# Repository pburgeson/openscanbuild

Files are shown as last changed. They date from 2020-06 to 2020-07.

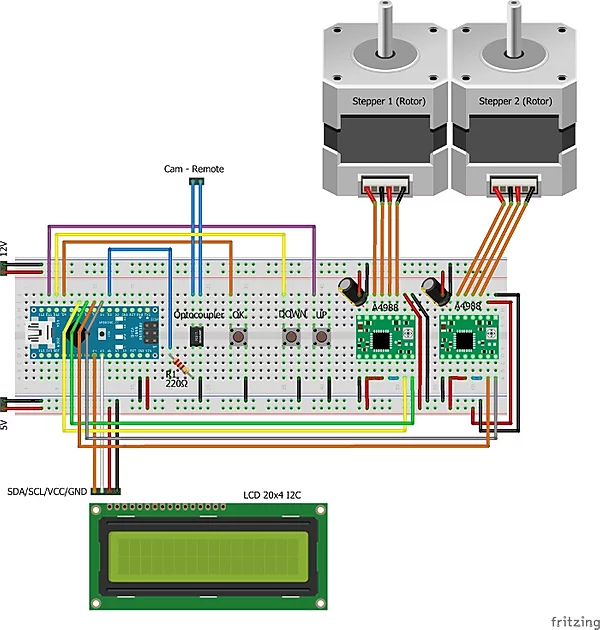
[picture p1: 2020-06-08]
Electronics/Breadboard - Schaltplan.webp

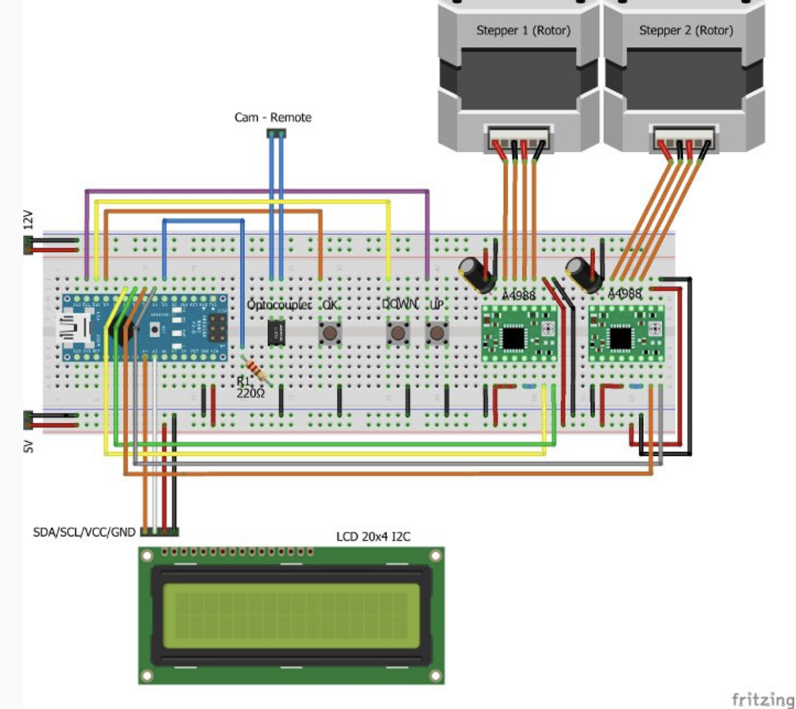
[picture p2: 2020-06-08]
Electronics/Openscan-fritzing.png

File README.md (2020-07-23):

# 3D Scanner Build
Build and testing of 3D scanner from Open Scan (https://en.openscan.eu/).  This is just using their plans and documents to successfully build a 3d scanner that uses photogrammetry.  My primary intent is to not have to measure objects that I want to design around in CAD.  Typically that means I'll be 3D printing the parts that make with it so precision is not incredibly critcal.  If I can get with +/- 0.010 in, I'll be pretty happy. 

A secondary goal is to develop processes and methods for updating github with project info and something akin to a project log.

# High Level Requirements
1. Able to generate 3D data that Autodesk Fusion 360 is capable of working with.
2. Precision of 0.010" or better
3. Scan Volume - Cylinder of 12 in diameter and height of 8 in
4. ~~Use of trinamic stepper drivers~~*
*Removed as open scan pcb was not compatible with Trinamic Step Stick and does not affect functionality

Future projects will include substantially more requirements development.  Since this project is about building a thing that someone else's design and documenting it, we won't go into a lot more detail.

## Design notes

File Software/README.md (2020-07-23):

# openscanbuild Software
2019_06-01_Scanner.ino - Arduino Sketch from openscan.eu
AccelStepper-1.59.zip - Arduino library for driving a stepper motor
NewLiquidCrystal_1.5.1.zip - Arduino library for lcd display
Scanner_Software_No_IRShutter - Arduino Sketch removing IR shutter due to difficulty in finding library
stepper_drive_step_dir_test - testing of stepper motor drive

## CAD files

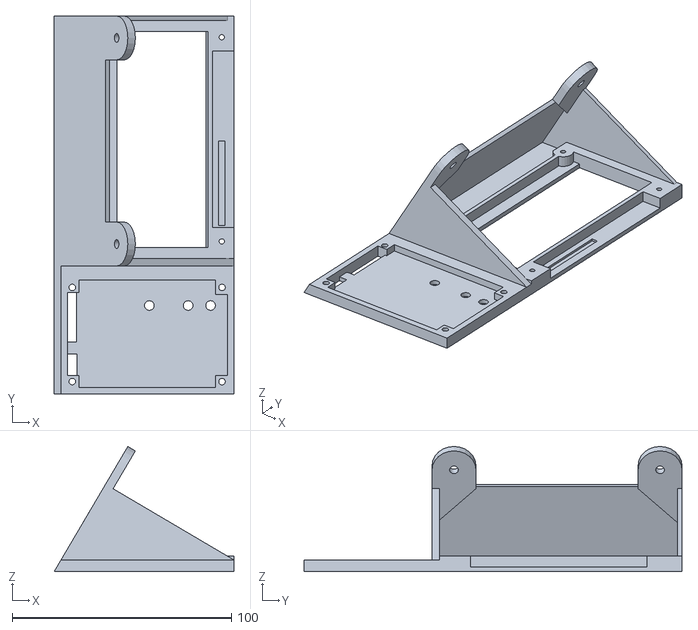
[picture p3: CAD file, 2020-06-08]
CAD Files/Control_module.stl
81.9 x 172.2 x 57.0

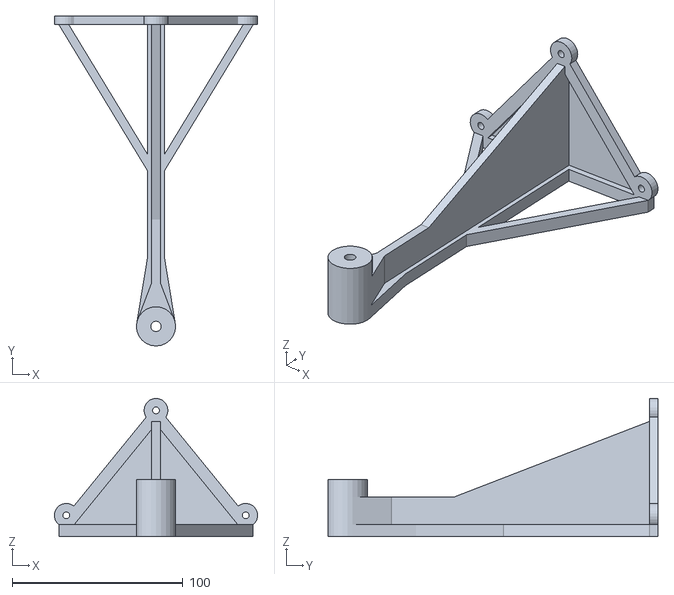
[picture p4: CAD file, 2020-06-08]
CAD Files/Stand2.stl
119.0 x 193.3 x 80.9

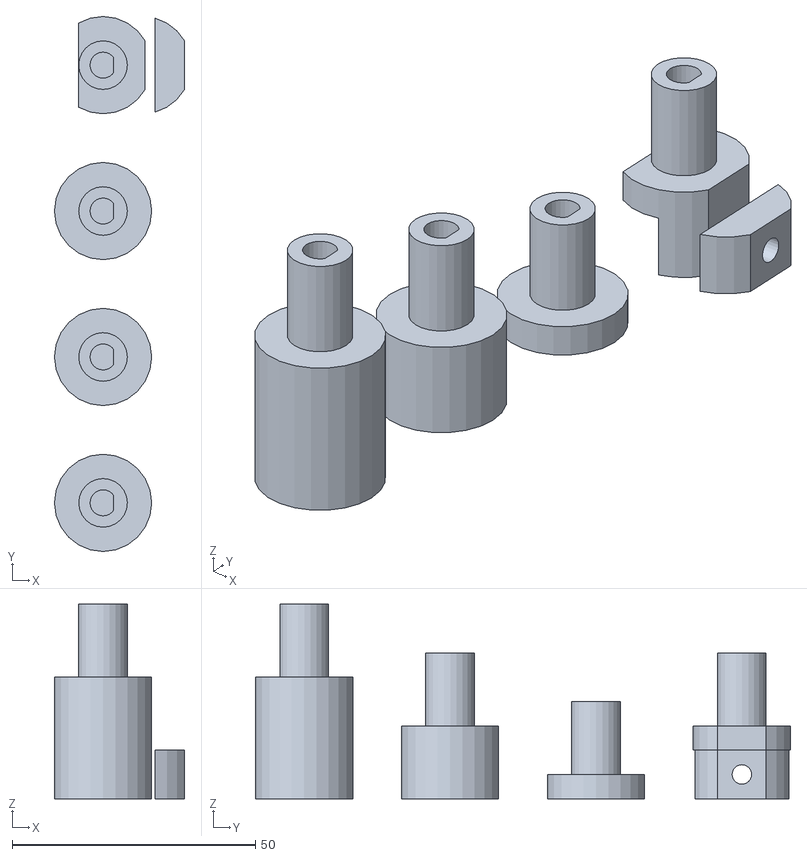
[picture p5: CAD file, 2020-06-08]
CAD Files/Turntable_-_Adapter_small.stl
26.8 x 110.0 x 40.0

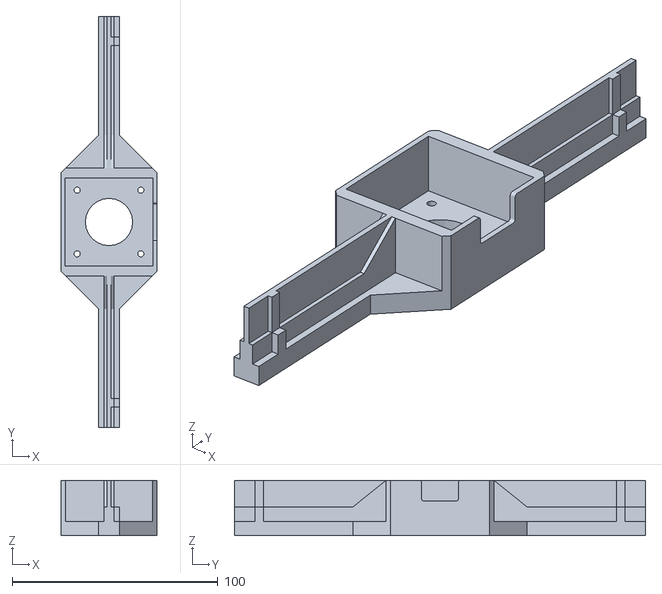
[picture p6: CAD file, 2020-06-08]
CAD Files/Turntable_Base_smallNema.STL
46.6 x 200.0 x 27.0

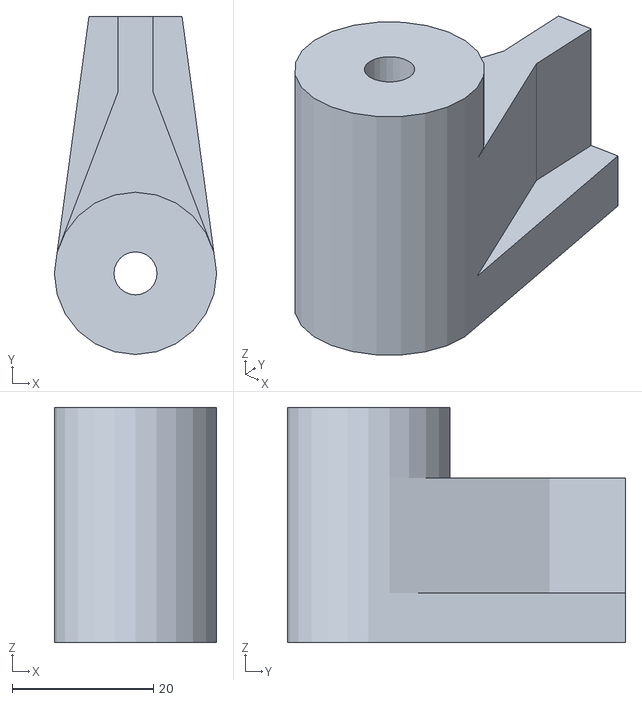
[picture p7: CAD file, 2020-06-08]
CAD Files/Stand1_-_Nema17 - Top.stl
23.0 x 47.9 x 33.3

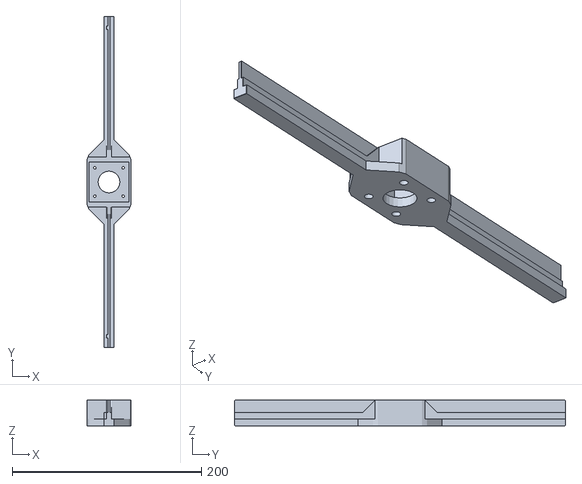
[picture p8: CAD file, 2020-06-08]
CAD Files/Turntable_Base_large_version_35cm.stl
47.0 x 350.0 x 27.0

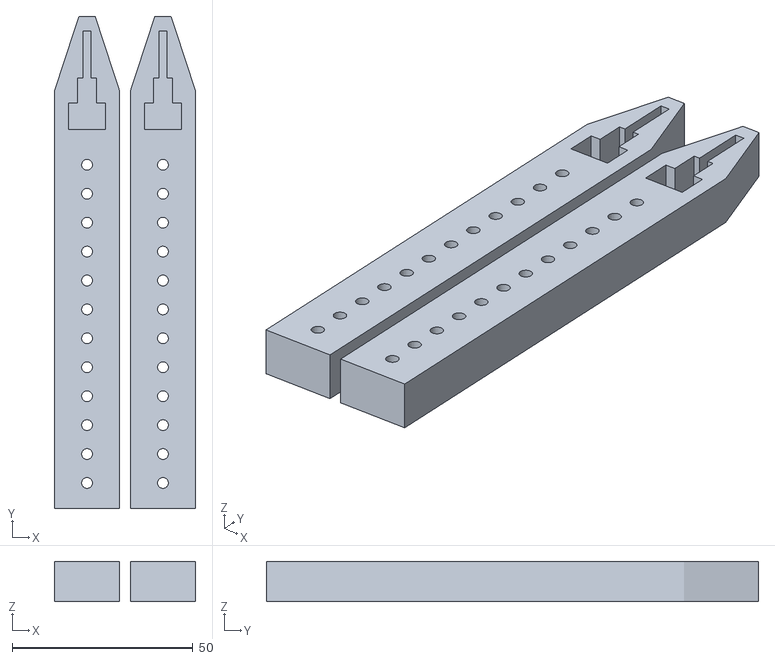
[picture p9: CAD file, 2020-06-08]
CAD Files/Rotary_Arm_-_2x.stl
39.0 x 136.2 x 11.2

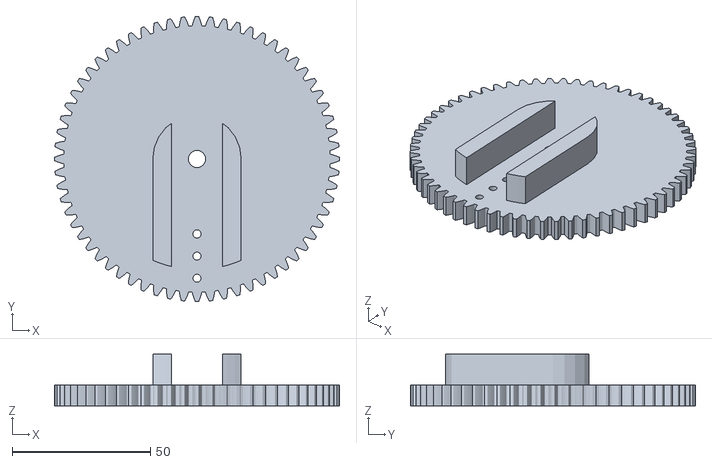
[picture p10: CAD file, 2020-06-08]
CAD Files/Adapter2_-_Gear_large.stl
103.1 x 103.1 x 18.7

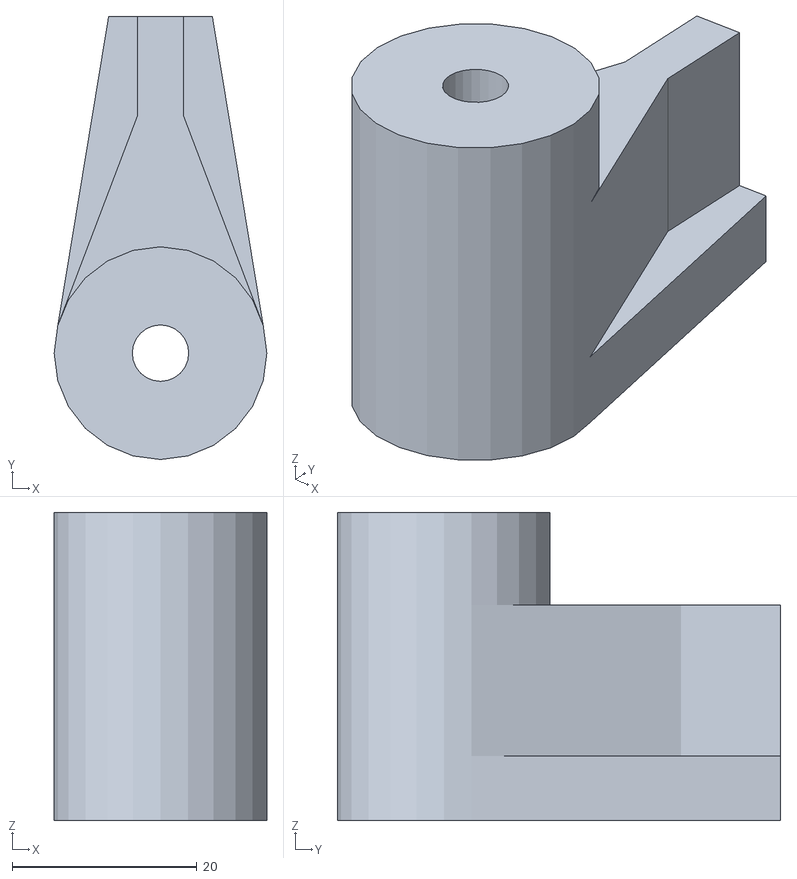
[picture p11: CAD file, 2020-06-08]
CAD Files/Stand2 - Top.stl
23.0 x 47.9 x 33.3

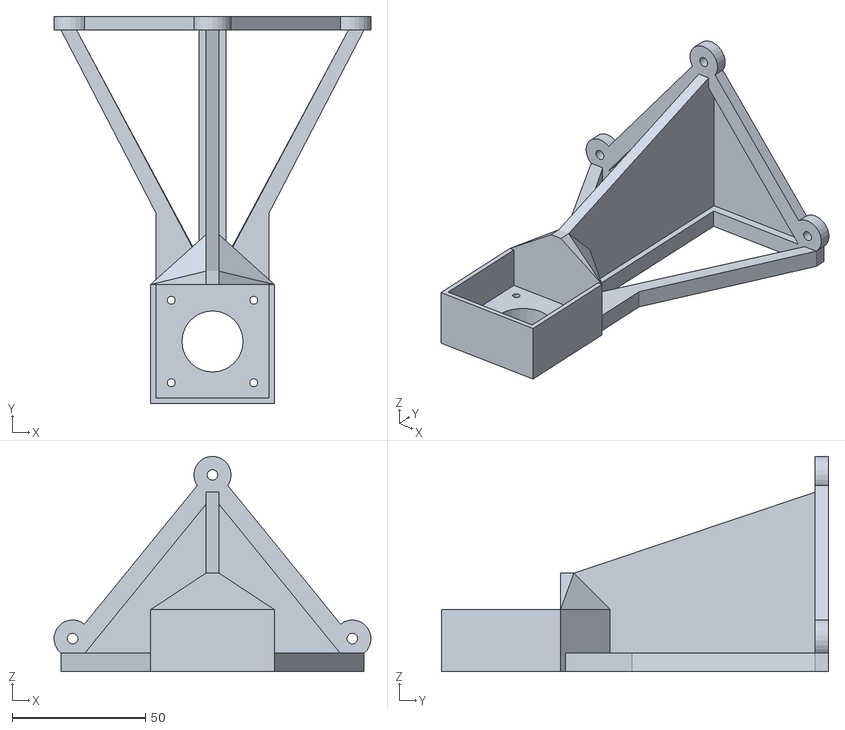
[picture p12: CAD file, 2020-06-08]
CAD Files/Stand1_-_Nema17 - Short.stl
119.0 x 145.4 x 80.9

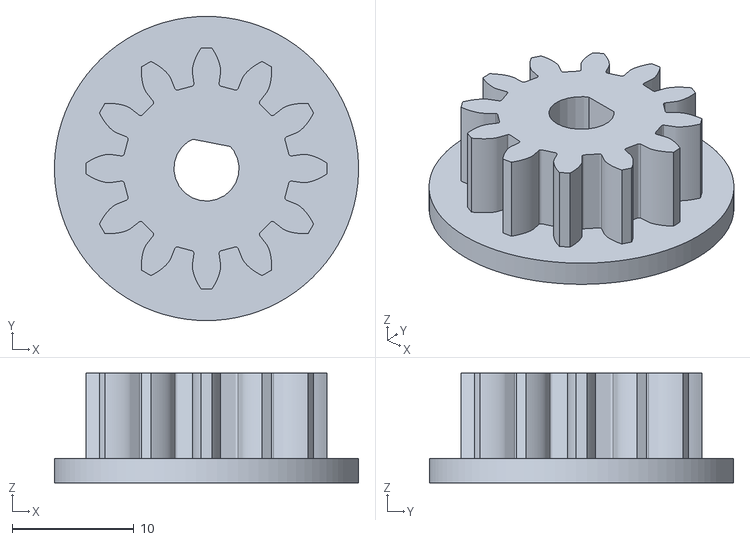
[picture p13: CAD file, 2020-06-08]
CAD Files/Gear_-_Small_v2.stl
25.0 x 25.0 x 9.00

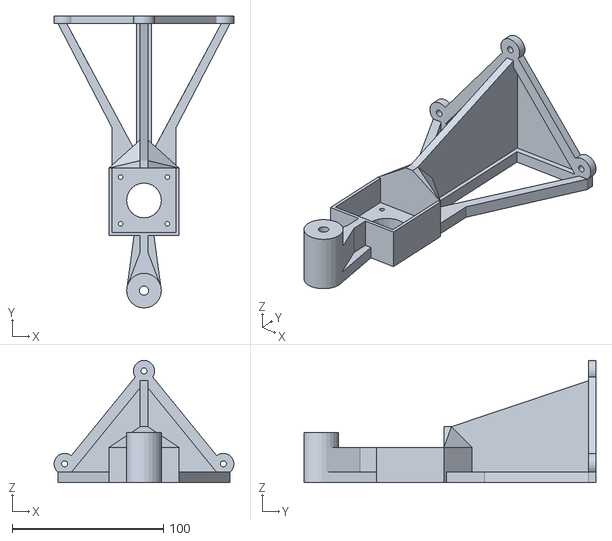
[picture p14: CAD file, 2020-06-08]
CAD Files/Stand1_-_Nema17.stl
119.0 x 193.3 x 80.9

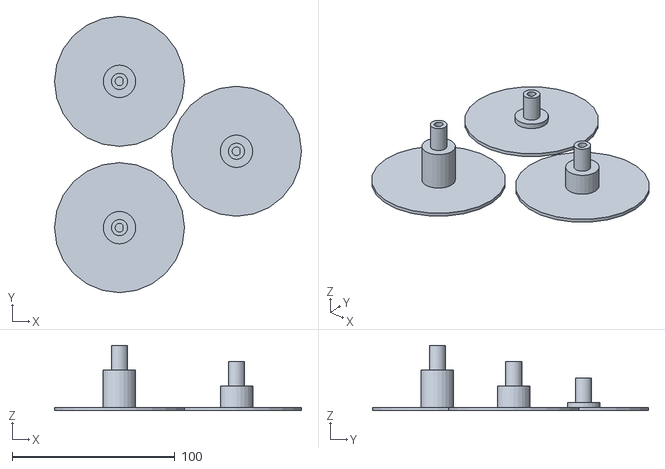
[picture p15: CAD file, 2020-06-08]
CAD Files/Turntable_-_Adapter_large.stl
152.0 x 170.0 x 40.0

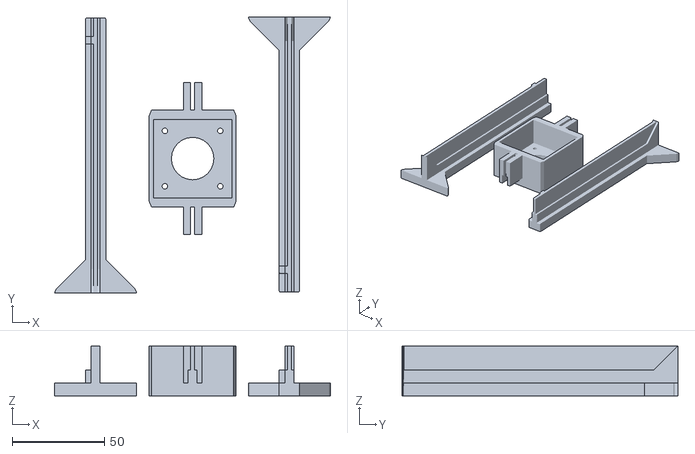
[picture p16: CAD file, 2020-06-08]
CAD Files/Turntable_Base_Large_Version_35cm_split_version_by_Paul.stl
149.4 x 149.3 x 27.0

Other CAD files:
CAD Files/Stand2 - Short.stl
CAD Files/Adapter1.stl
CAD Files/Gear_-_Small_v1.stl
CAD Files/Stand1_-_Nema17 v4.f3d
CAD Files/Stand2 v3.f3d

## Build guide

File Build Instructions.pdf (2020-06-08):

# OpenScan – User Manual

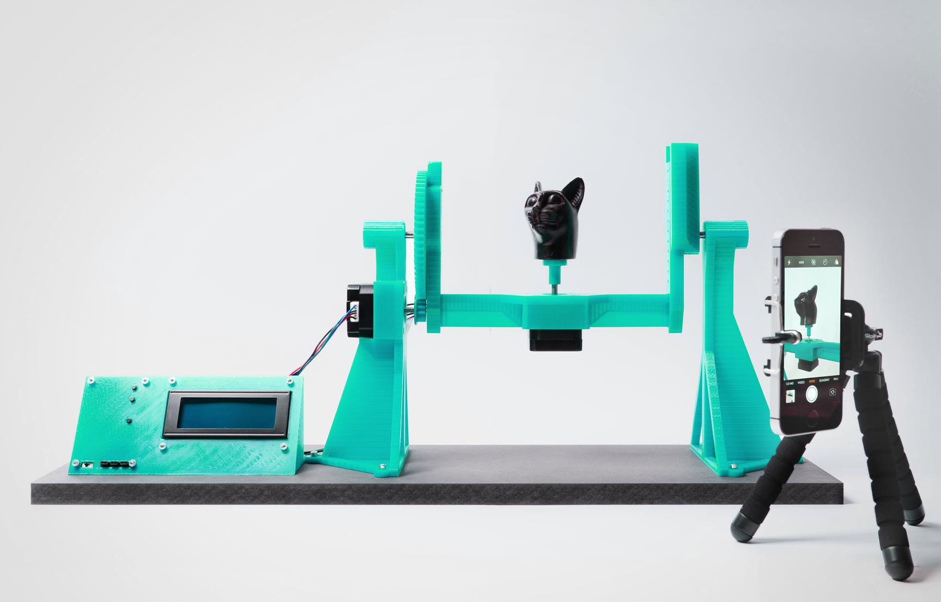
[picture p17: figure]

## Contents

## Material needed

M3 nut | 8
M3x12mm | 10
M3x8mm | 8
Steel pin (d=6mm, l>50mm) | 2
Jumper Wire 10cm m-f | 4
Nema 17 (min. 40Ncm) | 2
Stepper motor cable >70cm JST-XH-4P or 4P DuPont | 2
LCD 20x4 with I2C-Module | 1

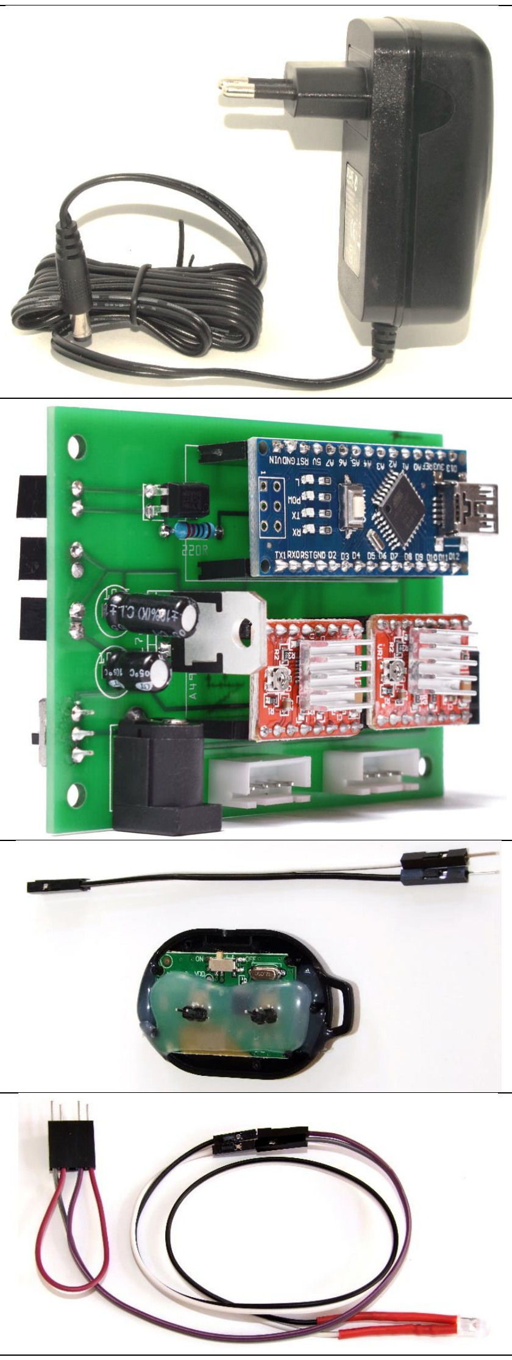
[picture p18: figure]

Power Supply 12V 2A Barrel connector (5,5mm-2,5mm) | 1
Control unit | 1
Remote Control Bluetooth (optional) | 1
Remote Control Infrared (optional) | 1

3D printable parts(https://www.thingiverse.com/thing:3050437/files)

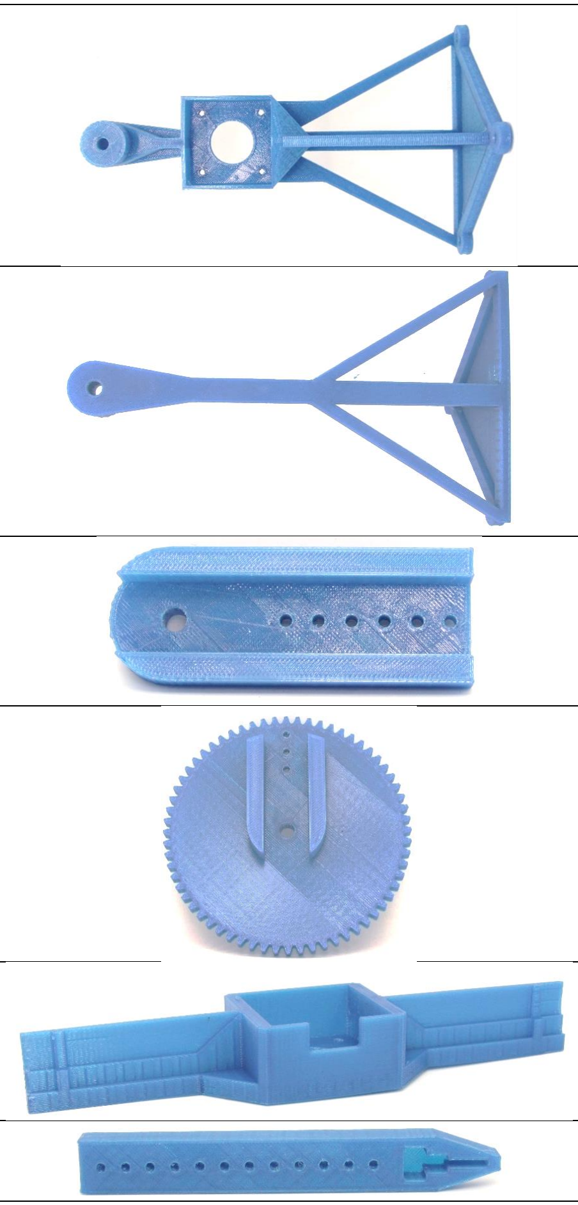
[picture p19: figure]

Stand1_Nema17.stl | 1
Stand2.stl | 1
Adapter1.stl | 1
Adapter2.stl | 1
Turntable_Base_Small.stl Optional:large-version | 1
Rotary_Arm.stl | 2

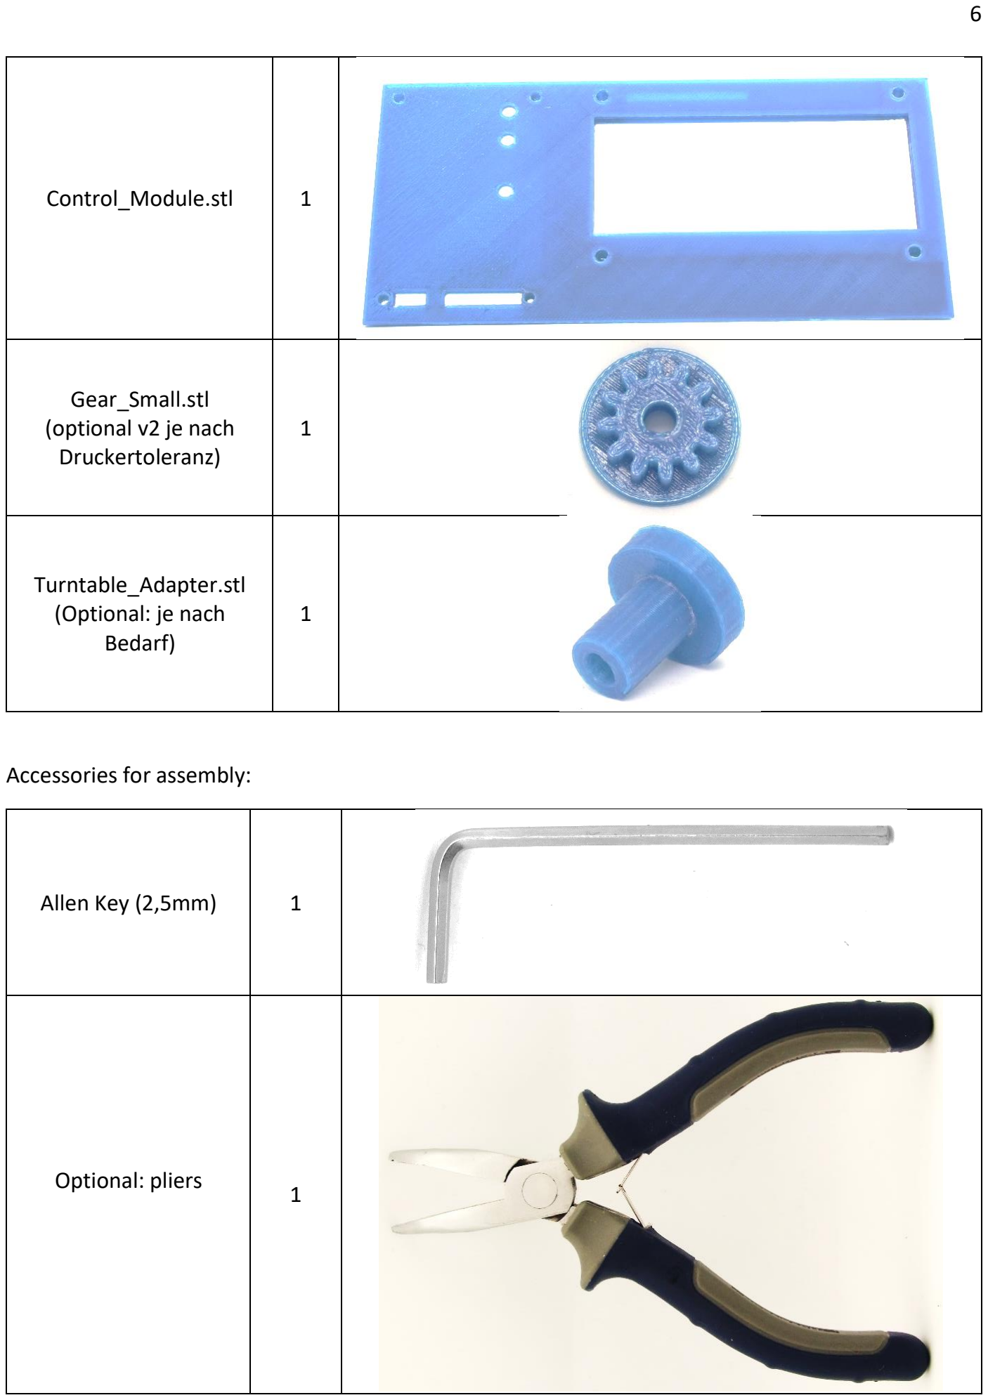
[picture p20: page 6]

Control_Module.stl | 1
Gear_Small.stl (optional v2 je nach Druckertoleranz) | 1
Turntable_Adapter.stl (Optional: je nach Bedarf) | 1

Accessories for assembly:

Allen Key (2,5mm) | 1
Optional: pliers | 1

## Assembly

### Step 1 – LCD

Needed parts:

- LCD 20x4 with I2C-Modul
- Control_module.stl
- M3x12 (4x)
- M3 nuts (4x)

Front:

Back:

Description:

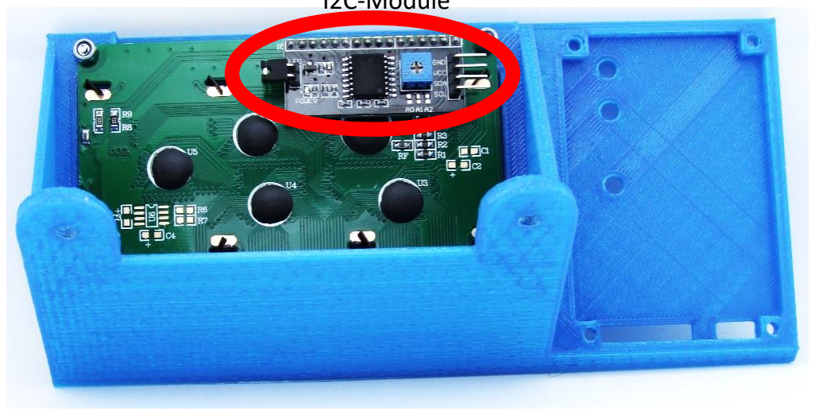
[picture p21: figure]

The display is mounted on the back of the control unit using four of the M3x12mm screws. See the orientation of the display - I2C module top right.

Note:

Depending on the printing accuracy, it may be necessary to pre-drill the screw holes with a 3mm drill bit.

I2C-Module

### Step 2 – Control unit

Needed parts:

- Control unit
- Control_module.stl (nach Schritt 1)
- M3x12 (4x)
- M3 nuts (4x)

Front:

Back:

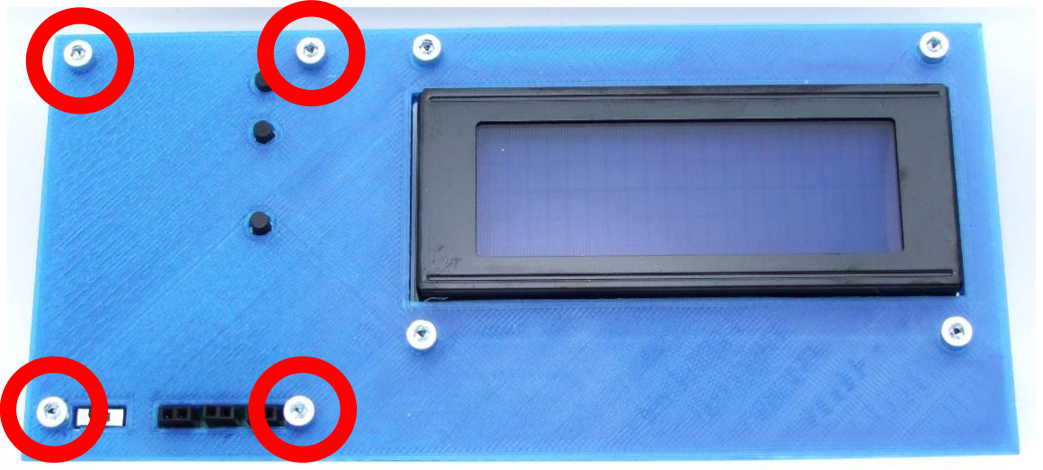
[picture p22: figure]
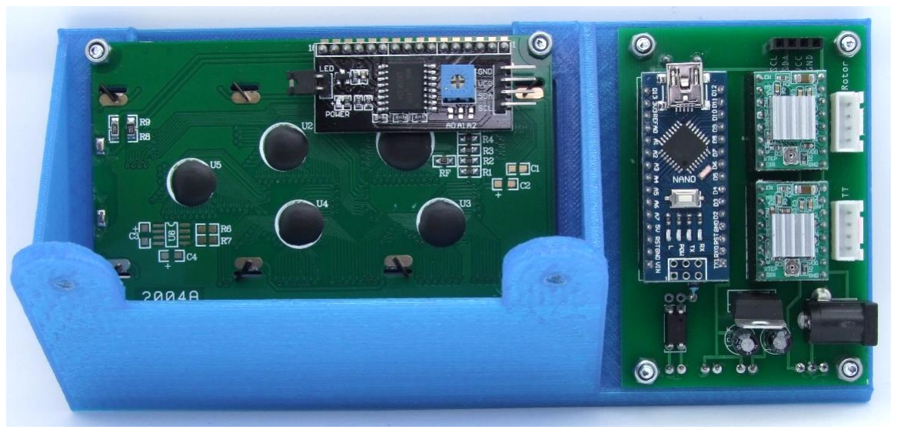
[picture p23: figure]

Description:

The control unit is mounted on the back of the printed unit using four of the M3x12mm screws.

Note:

Depending on the printing accuracy, it may be necessary to pre-drill the screw holes with a 3mm drill bit. It may also be necessary to deburr / enlarge the holes for the push buttons on the front.

### Step 3 – wiring the LCD

Needed parts:

- Control unit (after Step 2

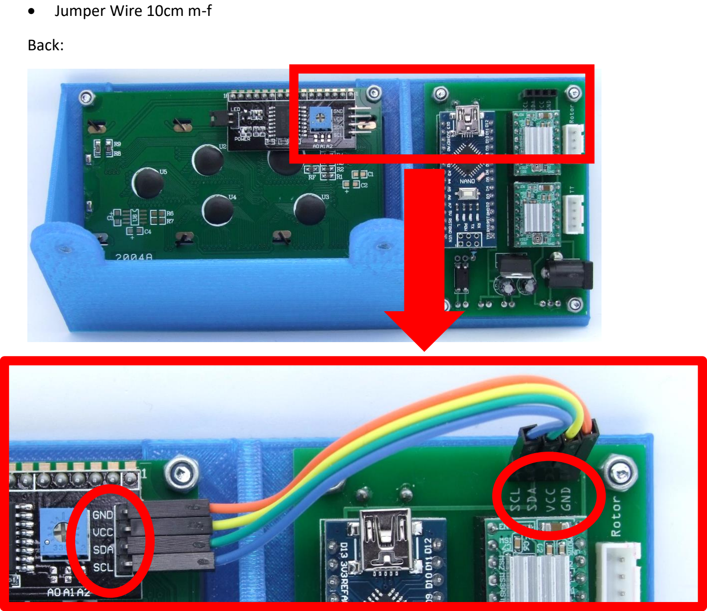
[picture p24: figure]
• Jumper Wire 10cm m-f; Back:

Description:

Wire the connections according to their labels. (GND-GND / VCC-VCC / SDA-SDA / SCL-SCL)

Important note:

This step should be double checked to ensure that the pins are properly connected, otherwise the control unit and / or the display can be destroyed!

### Step 4a – Stand 1

Needed parts:

- Stand1_Nema_17.stl
- Nema 17 (min. 40Ncm)
- M3x8mm (4x)
- Gear_Small.stl (optional v2)

Description:

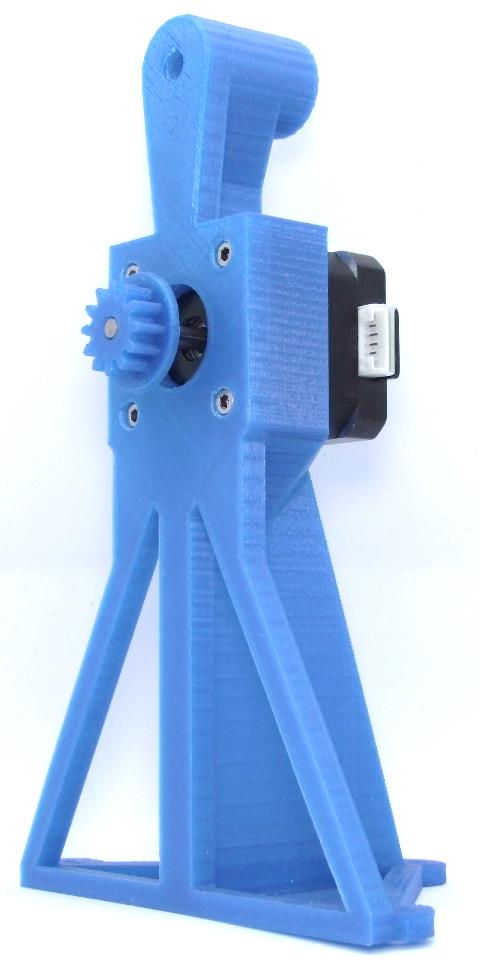
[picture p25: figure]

(1) Mount the stepper motor with four M3x8mm Screws onto the Stand1.stl.
(2) Press the Gear_small.stl onto the motor shaft. Make sure, that the gear and the motor shaft close flush at the front.

Note:

Depending on the printing accuracy, it may be necessary to pre-drill the screw holes with a 3mm drill bit. Furthermore the gear and the motor shaft might have a tight fit and you might have to „gently“ use the help of a hammer.

### Step 4b – Stand 1

Needed parts:

- Stand1_Nema_17.stl (after Step 4a)
- Adapter2.stl
- Steel pin (d=6mm, l>50mm)

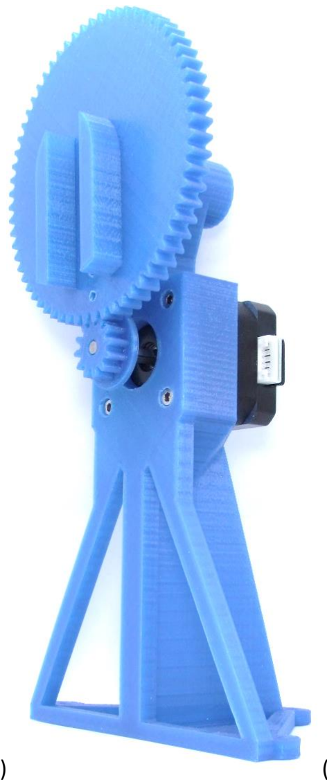
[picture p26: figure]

(1) | (2) | (3)

Description:

(1) The steel pin is pressed into the opening of the side stand.
(2) The larger gear (Adapter2.stl) is pressed onto the steel pin.
(3) The steel pin (top) and the motor shaft must NOT protrude forward from the components and should be flush with the surface. Superglue can be used to fix the position of the gears.

Note:

Both gears should match well and rotate relatively resistance free. If this is not the case, it may be necessary to replace the small gear with v2.stl or adjust the printer settings.

### Step 5 – Stand 2

Needed parts:

- Stand2.stl
- Adapter1.stl
- Steel pin (d=6mm, l>50mm)

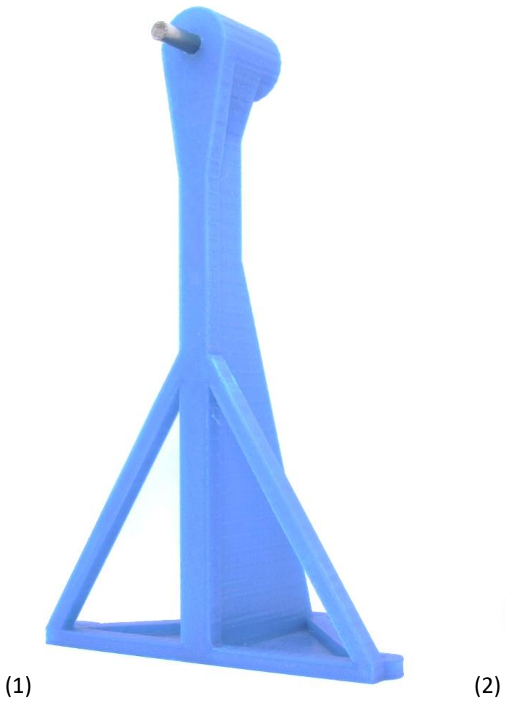
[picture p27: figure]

Description:

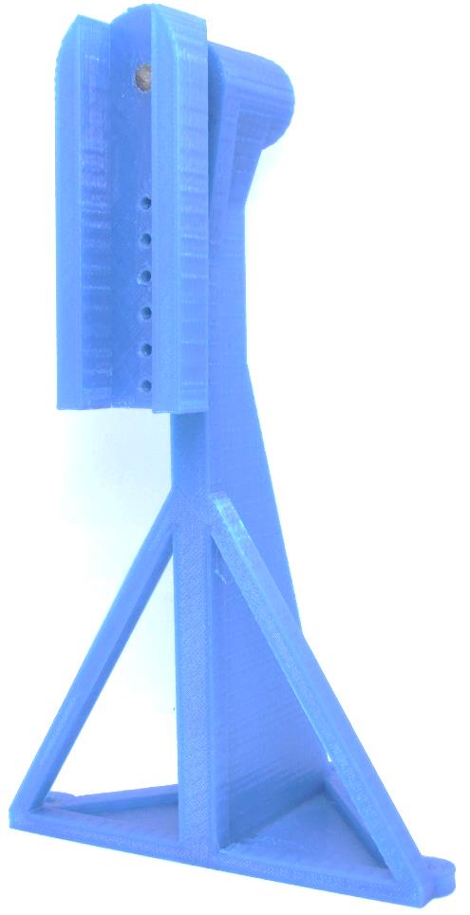
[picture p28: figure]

(1) The steel pin is pressed into the opening of the side stand
(2) The adapter1.stl is pressed onto the steel pin. It is important to ensure that the steel pin does not protrude forward from the adapter.

Note:

The adapter can be fixed with superglue on the steel pin. It must be ensured that the steel pin can rotate freely in the stand.

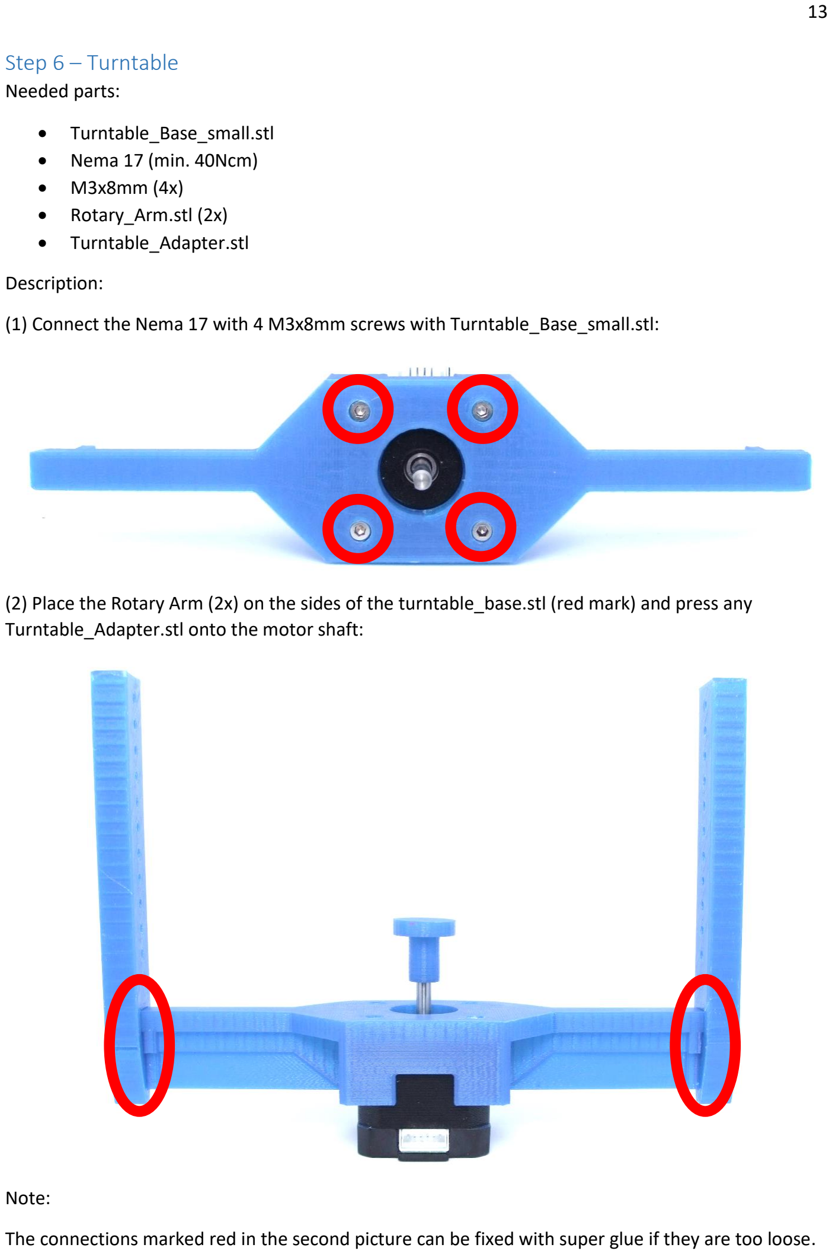
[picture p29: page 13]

### Step 6 – Turntable

Needed parts:

- Turntable_Base_small.stl
- Nema 17 (min. 40Ncm)
- M3x8mm (4x)
- Rotary_Arm.stl (2x)
- Turntable_Adapter.stl

Description:

(1) Connect the Nema 17 with 4 M3x8mm screws with Turntable_Base_small.stl:
(2) Place the Rotary Arm (2x) on the sides of the turntable_base.stl (red mark) and press any Turntable_Adapter.stl onto the motor shaft:

Note:

The connections marked red in the second picture can be fixed with super glue if they are too loose.

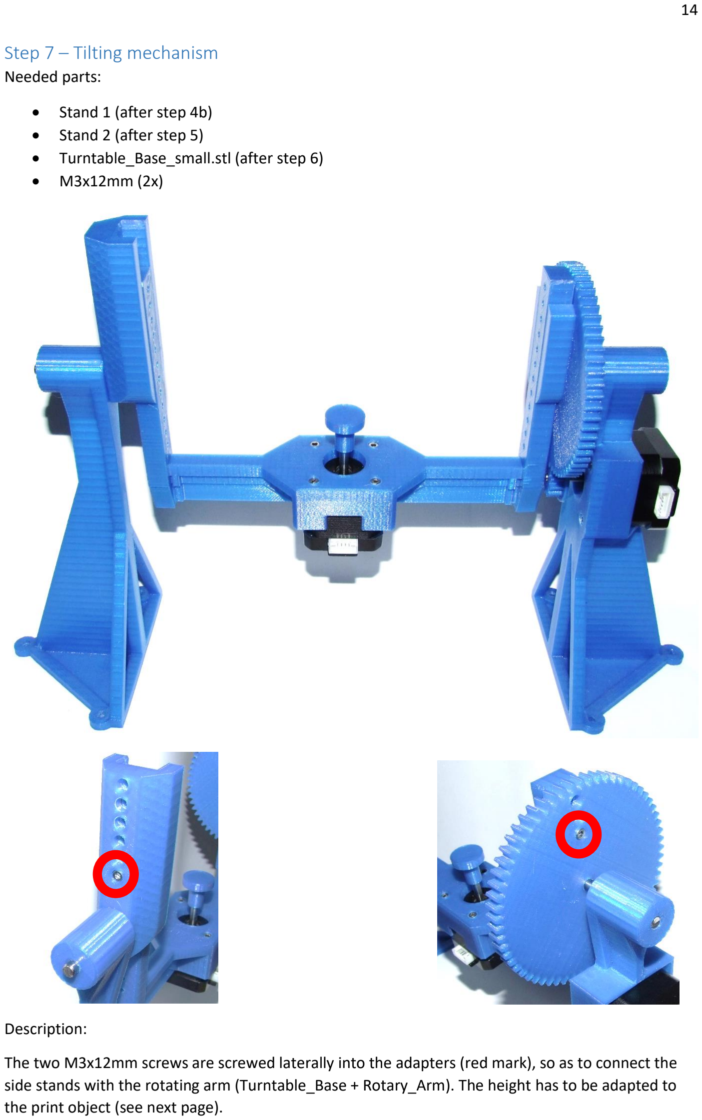
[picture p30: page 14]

### Step 7 – Tilting mechanism

Needed parts:

- Stand 1 (after step 4b)
- Stand 2 (after step 5)
- Turntable_Base_small.stl (after step 6)
- M3x12mm (2x)

Description:

The two M3x12mm screws are screwed laterally into the adapters (red mark), so as to connect the side stands with the rotating arm (Turntable_Base + Rotary_Arm). The height has to be adapted to the print object (see next page).

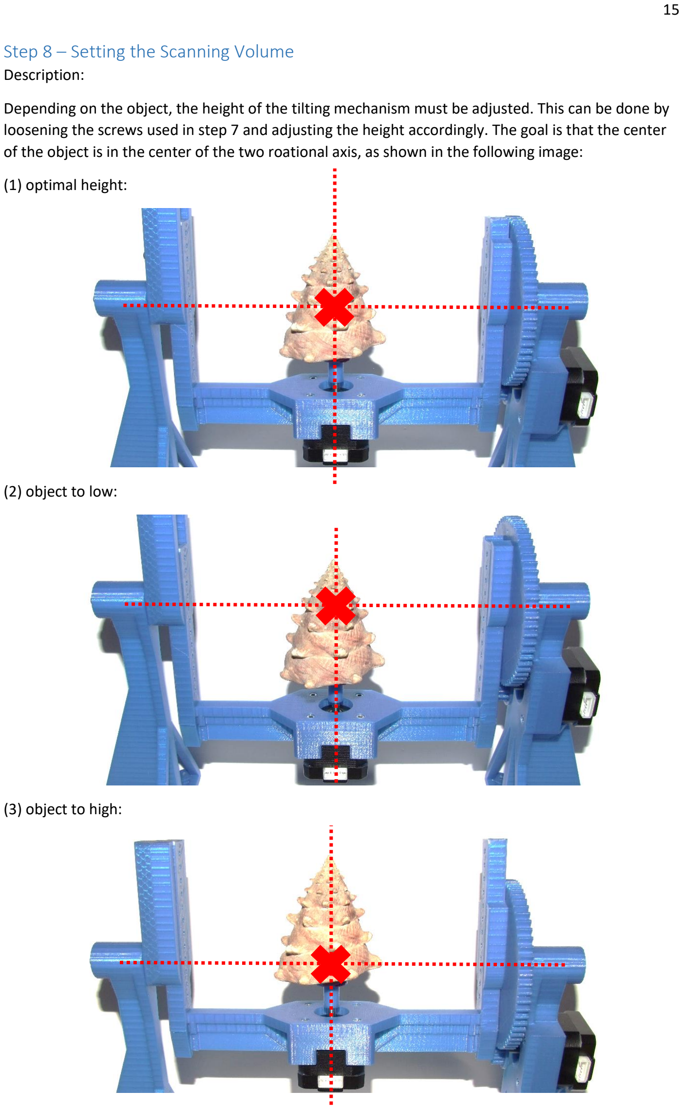
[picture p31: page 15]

### Step 8 – Setting the Scanning Volume

Description:

Depending on the object, the height of the tilting mechanism must be adjusted. This can be done by loosening the screws used in step 7 and adjusting the height accordingly. The goal is that the center of the object is in the center of the two roational axis, as shown in the following image:

(1) optimal height:
(2) object to low:
(3) object to high:

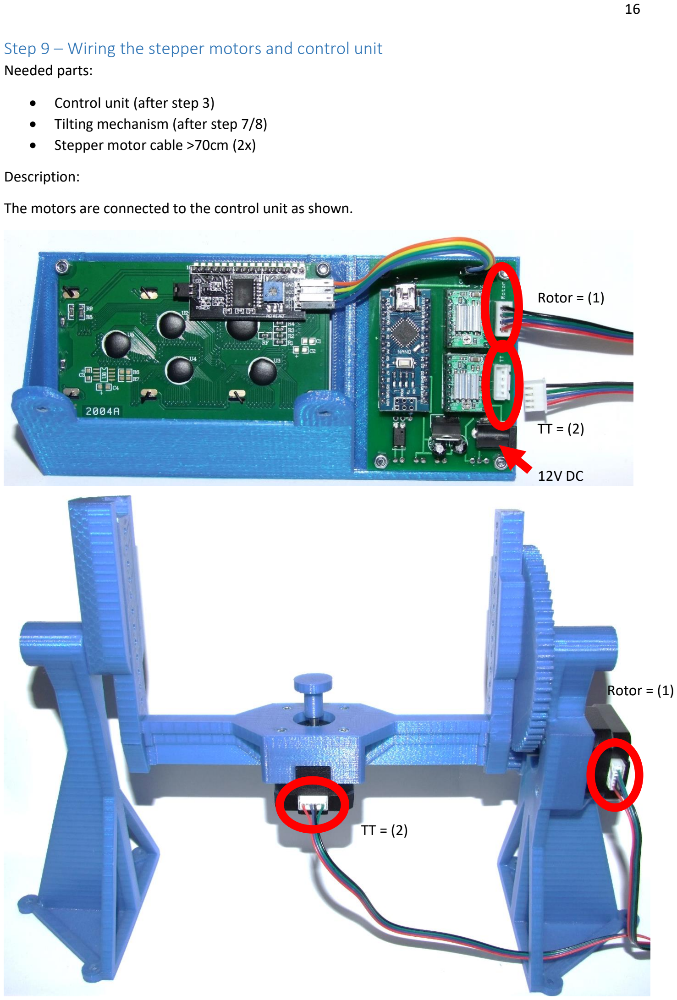
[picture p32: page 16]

### Step 9 – Wiring the stepper motors and control unit

Needed parts:

- Control unit (after step 3)
- Tilting mechanism (after step 7/8)
- Stepper motor cable >70cm (2x)

Description:

The motors are connected to the control unit as shown.

Rotor = (1)

TT = (2)

TT = (2)

Rotor = (1)

12V DC

### Step 10 – (optional) Mounting on a base plate / work surface

Needed parts:

- Tilting mechanism and control unit (after step 9)
- Screw for wood (d=3mm) or alternatively double-sided tape
- Wood panel (min. 600x150mm)

Description:

The tilting mechanism and the control unit are mounted on a base plate. This can be done either temporarily with double-sided tape or more durable with wood screws.

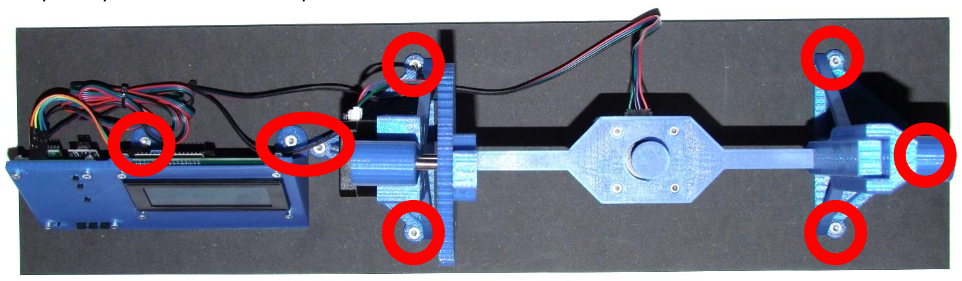
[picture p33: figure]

## Accessories

### Remote Control – Bluetooth for Android/iOS

A modified Bluetooth trigger can be used to trigger most smartphone cameras. The shown module is operated with a CR2032 button cell, which must be inserted on the back. As soon as the On / Off switch has been flipped, the blue LED lights up at regular intervals. The device must then be paired with the smartphone via Bluetooth. This can be done in the smartphone’s setting menu. The device should be visible as “AB Shutter 3” and has to be coupled accordingly

To connect the Bluetooth module to the control unit, the enclosed cables are used. The female DuPont plugs are plugged into the Bluetooth module. Attention: The upper connectors are for iOS, the lower for Android! (See picture below). You can test the functionality of the trigger by shorting the male ends of the cables.

The male DuPont plugs are then plugged into the outer-right two sockets on the control unit (Opto). Be careful choosing the right pins, as the wrong pins might destroy the bluetooth device!

Important: See Set Camera Mode / Trigger Mechanism to "direct"

Connector iOS

Connector Android

On/Off

Connector bluetooth

Male Dupont Pins (Opto)

LED - blue

Connector Pins (Opto)

### Remote Shutter Control – Infrared

Important: Set Camera mode to the appropriate camera model (settings menu)

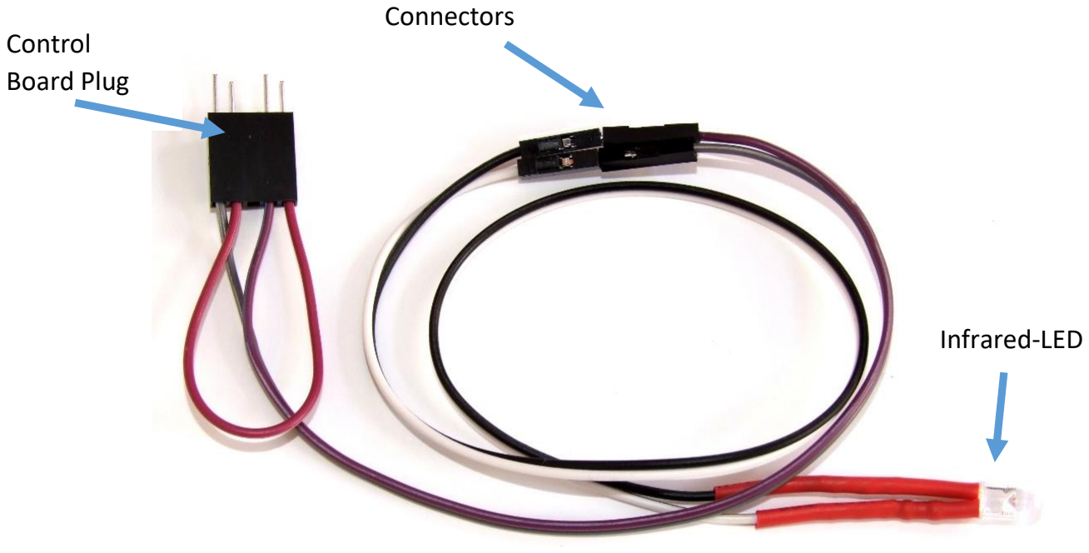
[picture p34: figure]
Control Board Plug; Connectors; Infrared-LED

Many cameras can be triggered by infrared. This function is to be activated in the corresponding menu of the camera (see user manual of your camera model). An infrared LED is connected to the control board of the scanner (see below) so that it emits a predefined light pulse at the given times. This light is not visible to the human eye (but not harmful either). You can sometimes see the light pulse as a slight pink flicker on the display of the camera, as the sensor of the camera registers the infrared light. However, some cameras (for example Iphones) use an infrared-filter, so the light pulses are not displayed. It should also be noted that these are very short light pulses (<0.1s). Note: If the camera does not detect a light pulse as soon as a scan routine is started, the connectors should be reversed.

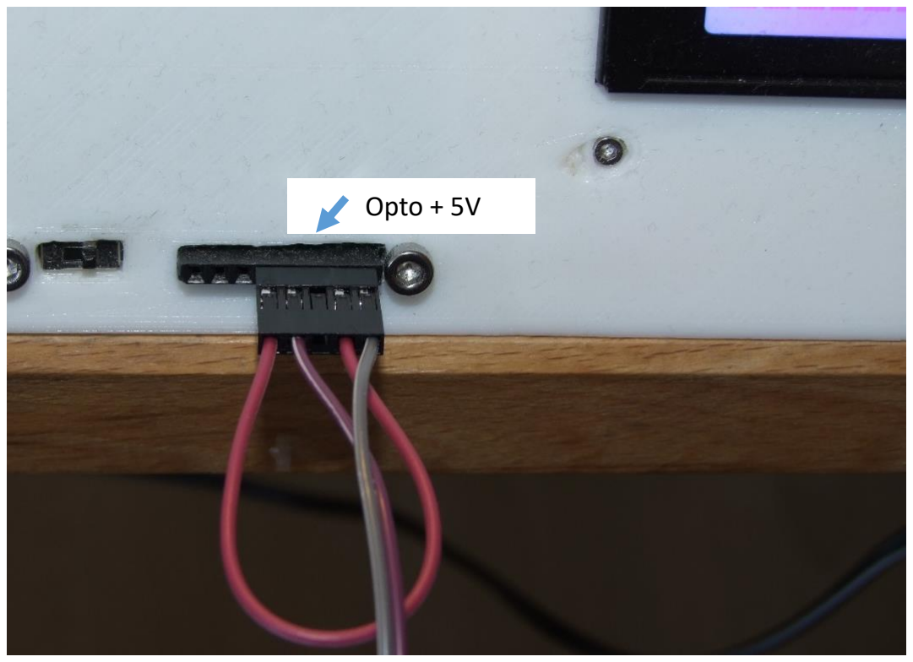
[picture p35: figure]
Opto + 5V

### Remote Shutter Control – Modifying a remote control

For (almost) all cameras you can buy a standard remote release, which can be connected to the camera by cable. These can be modified easily and also connected to the Scanner’s control unit. A very extensive source for various camera models and home-made remote releases is the following page: http://www.doc-diy.net/photo/remote_pinout/. A modified trigger can be connected to the control unit similar to the Bluetooth module (see: Remote control - Bluetooth for Android / iOS).

An existing remote release can be modified with minimal soldering skill and a total of two soldering points. The following pictures describe the basic procedure:

(1)-Remote Control for Nikon/Canon (ca. 5€) | (2) Opening the enclosure

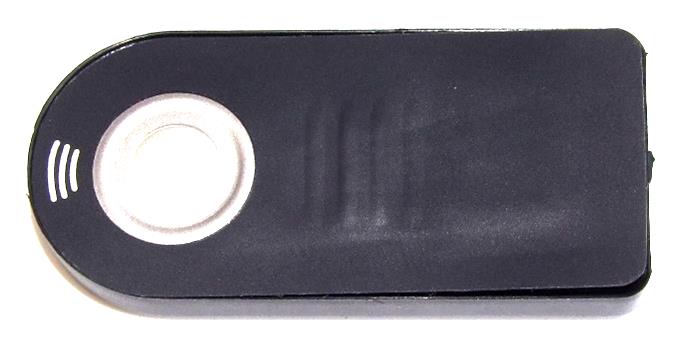
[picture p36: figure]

(3) Identification of the connectors

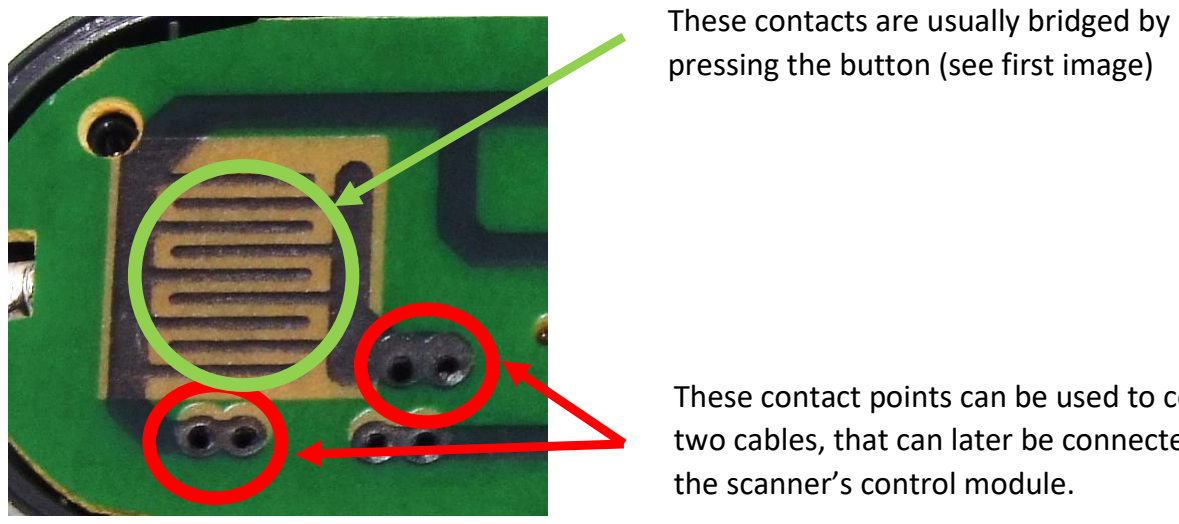
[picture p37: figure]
These contacts are usually bridged by pressing the button (see first image); the scanner’s control module.

(4) The shown points (red circles) have been contacted with two male jumper wires, that can be connected to the Scanner. By shortening the two wires the remote will send a pulse to the camera and trigger the shutter.

These contact points can be used to connect two cables, that can later be connected to

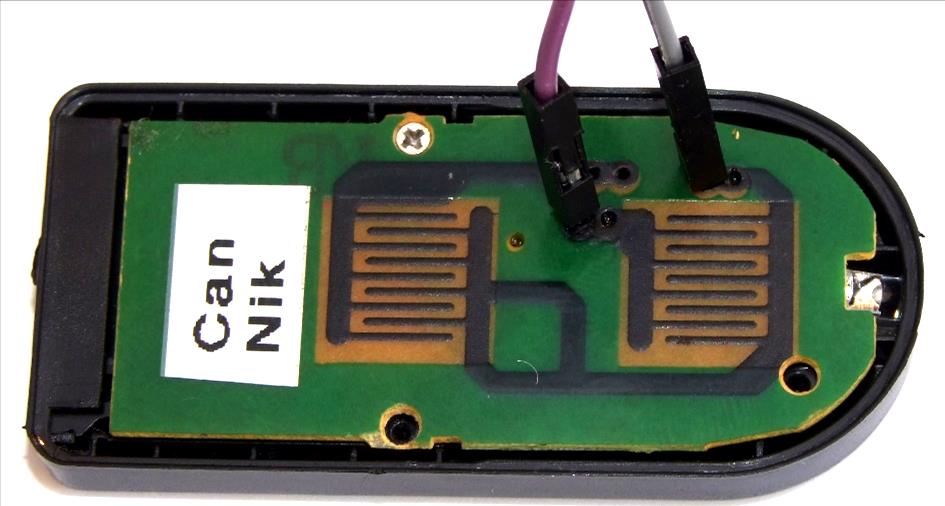
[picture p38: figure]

## Using the control unit (important notes!)

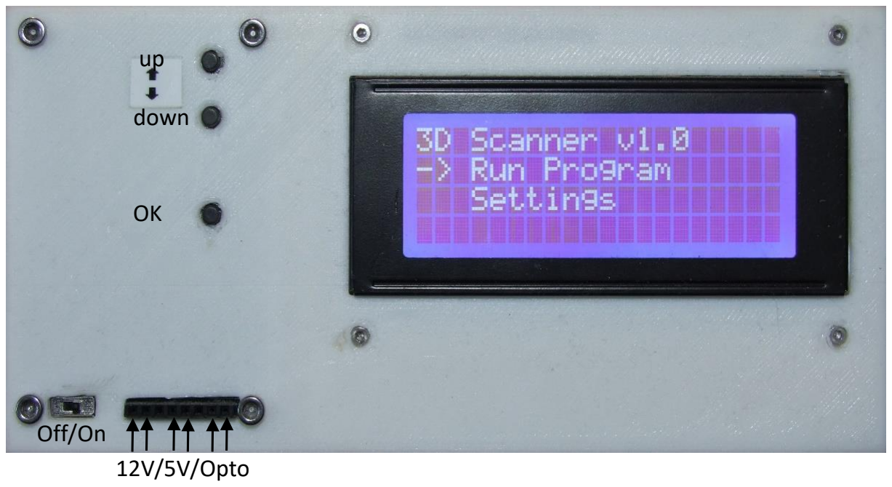
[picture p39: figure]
down; Off/On; 12V/5V/Opto

## Be careful not to mix up the 12V/5V/Opto connectors, when connecting any accessory to the control board as this might damage or destroy the devices!

### Main Menu

In the main menu, you can use the arrow keys to select whether a program should be loaded or started or whether settings of the scanner should be changed..

### Load/Start Program

The last used program or a saved program from the internal memory can be selected (up to twelve program sequences can be stored).
Select using the arrow keys up / down and confirm with OK.

Run last program
With the selection "Run Last Program" the last program is selected and the following screen appears.

To start this program, select "Start" with the arrow keys and confirm with OK. The parameters specify the following values:

Number of Photos per Rotation: 32

Start- und final tilting angle: 75°, i.e. the object is tilted to a maximum of + 75 ° and -75 ° from the starting position

Number of positions between start and end angle: 5, ie. at -75 °, -37,5 °, 0 °, + 37,5 ° and + 75 ° one turn of the turntable is made with 32 images. The transition between these angles is done in predefined steps, defined in Settings "min. vertical angle "- by default, an additional image is taken every 10° to simplify the alignment between the planes of rotation for the reconstruction software.

Load Program

There are up to twelve stored programs available, which can be customized in the "Settings" menu. For the explanation of the values see: "Run last program". The routine is selected via the arrow keys and confirmed with OK.

Then the program will ask again if the chosen program should be started.

Home – Rotor and Home – Turntable

At the beginning of each program routine, the zero position of the rotor (tilting mechanism) and the turntable can be selected by using the up / down buttons to select the appropriate position and confirm with OK.

The start of the program must be confirmed again. The Ok button then starts the routine.

Programmablauf
The progress of the routine is shown on the display

If the scan is finished or has been canceled, you can see the complete number of pictures taken:

Interrupt or Stop Routine

If a program is already running and you want to cancel it, the OK button must be held down (at least 1s) and the following screen appears. You will then be able to cancel the routine by pressing the Up button.

### Settings

In the settings menu you can use the arrow keys and confirm with OK to:

- change the individual routines ("modify program")
- set the waiting time per photo ("time per photo")
- choose the minimum angle between the rotation planes ("Min. Vert. Angle")
- choose the trigger mechanism ("Set Camera)

Modify Program
First, use the arrow keys to select the program to be changed and confirm with OK:

The parameters can be changed with the arrow buttons and confirmed with OK. First, choose the photos per turn of the turntable. The recommended value is 32. For primitive objects, 16 is also possible. Higher values should only be selected for very detailed objects, thereby the total number of photos will increase significantly.

Next, the start and end tilting angle are selected. Usually a maximum value of 45 ° works fine.

Next, the number of rotation planes between start and end tilting angle is determined. It is recommended that the planes are not more than 30° (better less) apart, i.e. that at a deflection of 30°

a value of three should be chosen. The scan arm is first tilted to -30 °, then to 0 ° and to + 30 °, and the preset number of photos is taken in each position.

Finally, you have to save the new program by selecting "Yes" and confirming with OK. The old program will be permanently overwritten.

Time per photo

Depending on the exposure and camera setting, this value should be adjusted using the arrow keys. The value indicates how much time is given to the camera after triggering to take the photo. The value varies depending on the camera and settings and is set to 2.5s by default. If you reduce this value, the entire program runtime can be significantly shortened. Caution: If the value is too small, the pictures will be blurred! After confirming the value with OK, you immediately return to the main menu and the value will be saved! – better check twice :)

Min. vertical angle

This value defines the angle between two planes of rotation without taking additional photos. As a rule of thumb, this value does not have to be adjusted and can stay 10 °. If, for example, you have the following program 16 photos/25°/2 positions, the turntable will rotate at a tilting of + 25 °, as well as at -25 °. However, since there is too much space between these two angles, the program will take an additional photo at + 15 °, + 5 °, -5 °, and -15 ° so that the reconstruction software can later better align the different layers.

Set Camera mode / Triggering mechanism
In this menu, the type of camera activation is selected. With the OK button the (changed) settings are saved immediately and you return to the main menu. Currently, basically two triggering mechanisms are supported, which can be selected using the arrow keys and selected by OK.
(1) „direct“ – Direct triggering by shorting two pins on the front of the control unit (opto). These can be connected, for example, with an external remote shutter control unit, so that the Arduino quasi takes over the button of the trigger. This option should be selected if e.g. the Bluetooth smartphone trigger or any modified remote control is being used.
(2) „Canon“/“Sony“/“Pentax“/“Olympus“/“Nikon“/“Minolta“ – Infrared-Remote based on Sebastian Setz Arduino Library multiCameraIrControl.h

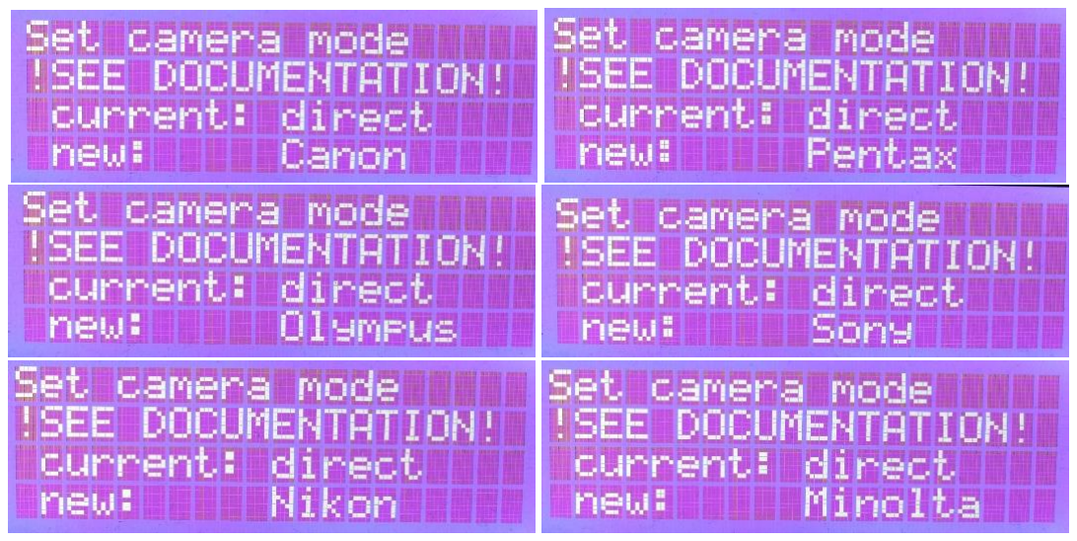
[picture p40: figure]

Unfortunately, Sebastian Setz's project ended a while ago, so it's currently not possible to say which camera models work and can be triggered with the implemented infrared pulses. After our research, at least the following models are supported. However, it is very likely that other models of similar series will work as well:

Canon EOS: 350D, 450D, 550D, 600D, 700D, M, D5 Mark II, D6, D7

Minolta: F300

Nikon: D3000, D7000, D40, D50, D80, D90

Olympus: E-3, E-300, E-410, E-510

Pentax: K10, K100D Super, K200D, K7, S1, WG-1, X5

Sony: Alpha 330, Alpha 380, Alpha 580, CX730, NEX 5N

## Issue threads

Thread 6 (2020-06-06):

Modify bluetooth shutter

pburgeson, 2020-06-06:

pburgeson, 2020-06-06:
Page 18 of build instructions

pburgeson, 2020-07-23:
Soldered pins to button on bluetooth shutter.  tested and seems to work

Closed 2020-07-23.

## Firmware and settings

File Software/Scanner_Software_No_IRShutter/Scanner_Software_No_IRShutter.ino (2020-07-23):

#include <EEPROM.h>
#include <Wire.h>
#include <LCD.h>
#include <LiquidCrystal_I2C.h>
//#include <multiCameraIrControl.h>
#include <AccelStepper.h>

int cursor = 1;
byte error, add;
int I2C;
int val;
int val1;
int val2;
int val3;
int val4;
int FpR; // Fotos per Rotation
int Startangle; //Vertical startangle
int Positions; //number of vertical positions
int TpF; //Time per Foto
int minVert; //minimal vertical angle
int menu;
int buttonUP = 11; //pin for button up
int buttonDOWN = 10; //pin for button down
int buttonOK = 9; //pin for button ok
int step1startpin = 7; //Stepper1 start pin
int step2startpin = 4; //Stepper2 start pin
int photopin1 = 3; //CameraPin
int step1dirpin = 4; //Stepper1 direction pin
int step2dirpin = 6; //Stepper2 direction pin
int step1steppin = 5; //Stepper1 step pin
int step2steppin = 7; //Stepper2 step pin
int SpR1 = 3200; //Steps per Revolution (Stepper1)
int SpR2 = 16000; //Steps per Revolution (Stepper2)
int totalphotos =0;
int releasetime = 100; // 1500ms for cam and 300 for iphone



AccelStepper Stepper1(1, step1steppin, step1dirpin); // TABLE!!
AccelStepper Stepper2(1, step2steppin, step2dirpin); //(ROTOR!!!)

void setup() {

    Serial.begin(9600);
 
  Wire.begin();  ////////////////////////////////////////////////////////////Scanning LCD I2C Address - LCD Setup
  for(add = 1; add < 127; add++ )
  {
    Wire.beginTransmission(add);
    error = Wire.endTransmission();
 
    if (error == 0)
    { I2C=add;
      add=128;
    }
  }
  #define address I2C
  LiquidCrystal_I2C  lcd(address, 2, 1, 0, 4, 5, 6, 7);
  lcd.begin (20, 4); 
  lcd.setBacklightPin(3, POSITIVE);
  lcd.setBacklight(HIGH);
  lcd.home ();

  Stepper1.setMaxSpeed(1000); //set max speed the motor will turn (steps/second)   //KREIS
  Stepper1.setAcceleration(200); //set acceleration (steps/second^2)
  Stepper2.setMaxSpeed(5000); //set max speed the motor will turn (steps/second)   // TURNTABLE
  Stepper2.setAcceleration(1000); //set acceleration (steps/second^2)
  Stepper1.setCurrentPosition(0);
  Stepper2.setCurrentPosition(0);

  pinMode(buttonUP, INPUT_PULLUP);
  pinMode(buttonDOWN, INPUT_PULLUP);
  pinMode(buttonOK, INPUT_PULLUP);

  pinMode(photopin1,OUTPUT);

  // FIRST SETUP EVER //
  if (EEPROM.read(1) != 103 || EEPROM.read(2) != 101 || EEPROM.read(3) != 101) {
    lcd.clear();
    delay(100);
    lcd.setCursor(0, 0);
    lcd.print("initializing");
    delay(100);
      
    EEPROM.write(4, 25);
    EEPROM.write(5, 4);
    EEPROM.write(6, 4);
    EEPROM.write(7, 10);
    EEPROM.write(100, 1);
    EEPROM.write(101, 16);
    EEPROM.write(102, 0);

    EEPROM.write(8, 16); EEPROM.write(9, 0); EEPROM.write(10, 1);
    EEPROM.write(11, 32); EEPROM.write(12, 0); EEPROM.write(13, 1);
    EEPROM.write(14, 64); EEPROM.write(15, 0); EEPROM.write(16, 1);

    EEPROM.write(17, 16); EEPROM.write(18, 25); EEPROM.write(19, 3);
    EEPROM.write(20, 16); EEPROM.write(21, 50); EEPROM.write(22, 3);
    EEPROM.write(23, 16); EEPROM.write(24, 75); EEPROM.write(25, 3);

    EEPROM.write(26, 16); EEPROM.write(27, 25); EEPROM.write(28, 5);
    EEPROM.write(29, 16); EEPROM.write(30, 50); EEPROM.write(31, 5);
    EEPROM.write(32, 16); EEPROM.write(33, 75); EEPROM.write(34, 5);

    EEPROM.write(35, 32); EEPROM.write(36, 25); EEPROM.write(37, 3);
    EEPROM.write(38, 32); EEPROM.write(39, 50); EEPROM.write(40, 5);
    EEPROM.write(41, 32); EEPROM.write(42, 75); EEPROM.write(43, 5);
    
    EEPROM.write(44, 1);

    EEPROM.write(1, 103);
    EEPROM.write(2, 101);
    EEPROM.write(3, 101);


  }
  menu = 1;
  }

void loop() {

  #define address I2C
  LiquidCrystal_I2C  lcd(address, 2, 1, 0, 4, 5, 6, 7);
  lcd.begin (20, 4); 
  lcd.setBacklightPin(3, POSITIVE);
  lcd.setBacklight(HIGH);
  while(1){
  while (menu != 0) {

    if (menu == 1) {             ///////////////////////////////////////// 1 Main Menu //
      cursor = 1;
      lcd.clear();
      lcd.setCursor(0, 0);
      lcd.print("3D Scanner v1.0");
      lcd.setCursor (0, 1);
      lcd.print("-> Run Program");
      lcd.setCursor (3, 2);
      lcd.print("Settings");
      while (digitalRead(buttonOK) == LOW) {
        delay(10);
      }
      while (digitalRead(buttonOK) == HIGH) {
        if (digitalRead(buttonDOWN) == LOW && cursor < 2) {
          lcd.setCursor(0, cursor);
          lcd.print("  ");
          cursor = cursor + 1;
          lcd.setCursor(0, cursor);
          lcd.print("->");
          delay(300);
        }
        if (digitalRead(buttonUP) == LOW && cursor > 1) {
          lcd.setCursor(0, cursor);
          lcd.print("  ");
          cursor = cursor - 1;
          lcd.setCursor(0, cursor);
          lcd.print("->");
          delay(300);
        }
      }
      if (cursor == 1) {
        menu = 2;
      }
      if (cursor == 2) {
        menu = 3;
      }
      delay(300);
    }

    if (menu == 2) {                   ////////////////////////////////////////// 2 Run Program //
      lcd.clear();
      lcd.setCursor(0, 0);
      lcd.print("-> Run last Program");
      lcd.setCursor(3, 1);
      lcd.print("Load Program");
      lcd.setCursor(3, 2);
      lcd.print(" back");
      cursor = 0;
      while (digitalRead(buttonOK) == LOW) {
        delay(10);
      }
      while (digitalRead(buttonOK) == HIGH) {
        if (digitalRead(buttonDOWN) == LOW && cursor < 2) {
          lcd.setCursor(0, cursor);
          lcd.print("  ");
          cursor = cursor + 1;
          lcd.setCursor(0, cursor);
          lcd.print("->");
          delay(300);
        }
        if (digitalRead(buttonUP) == LOW && cursor > 0) {
          lcd.setCursor(0, cursor);
          lcd.print("  ");
          cursor = cursor - 1;
          lcd.setCursor(0, cursor);
          lcd.print("->");
          delay(300);
        }
      }
      if (cursor == 0) {
        menu = 21;
      }
      if (cursor == 1) {
        menu = 22;
      }
      if (cursor == 2) {
        menu = 1;
      }
      delay(300);
    }

    if (menu == 3) {             ///////////////////////////////////////////////// 3 Settings Main
      lcd.clear();
      lcd.setCursor(0, 0);
      lcd.print("-> Modify Program");
      lcd.setCursor(3, 1);
      lcd.print("Time per Photo");
      lcd.setCursor(3, 2);
      lcd.print("Min. Vert. Angle");
      lcd.setCursor(3, 3);
      lcd.print("Set Camera   BACK");
      cursor = 0;

      while (digitalRead(buttonOK) == LOW) {
        delay(10);
      }
      while (digitalRead(buttonOK) == HIGH) {
          lcd.setCursor(0, cursor);
          lcd.print("  ");
          delay(150);
          if (cursor<4){
            lcd.setCursor(0, cursor);
            lcd.print("->");
            delay(150);
            lcd.setCursor(0,cursor);
            lcd.print("  ");
          }
          if (cursor==4){
            lcd.setCursor(16,3);
            lcd.print("    ");
            delay(150);
            lcd.setCursor(16,3);
            lcd.print("BACK");
          }

        if (digitalRead(buttonDOWN) == LOW && cursor < 5) {
          cursor = cursor + 1;
        }
        if (digitalRead(buttonUP) == LOW && cursor > -1) {
          cursor = cursor - 1;
        }
        if(cursor==5){cursor=0;}
        if(cursor==-1){cursor=4;}
        
      }
      if (cursor == 0) {
        menu = 23;
      }
      if (cursor == 1) {
        menu = 31;
      }
      if (cursor == 2) {
        menu = 34;
      }
      if (cursor == 3) {
        menu =35;                      
      }
      if (cursor == 4) {
        menu = 1;
      }
    }

    if (menu == 21) {    /////////////////////////////////////////////////////// 2.1 Run Last Program
      val1 = EEPROM.read(100);
      val2 = EEPROM.read(101);
      val3 = EEPROM.read(102);
      lcd.clear();
      lcd.setCursor(0, 0);
      lcd.print("Last Program");
      lcd.setCursor(1, 1);
      lcd.print("(Photos/Angle/Pos.)");
      lcd.setCursor(1, 2);
      lcd.print("(");
      lcd.print(val1);
      lcd.print(" / ");
      lcd.print(val2);
      lcd.print(" / ");
      lcd.print(val3);
      lcd.print(")");
      lcd.setCursor(0, 3);
      lcd.print("START           BACK");
      cursor = 2;
      while (digitalRead(buttonOK) == LOW) {
        delay(10);
      }
      while (digitalRead(buttonOK) == HIGH) {
        while (cursor == 2 && digitalRead(buttonOK) == HIGH) {
          lcd.setCursor(16, 3);
          lcd.print("    ");
          delay(100);
          lcd.setCursor(16, 3);
          lcd.print("BACK");
          delay(200);
          if (digitalRead(buttonUP) == LOW) {
            cursor = 1;
          }
        }
        while (cursor == 1 && digitalRead(buttonOK) == HIGH) {
          lcd.setCursor(0, 3);
          lcd.print("     ");
          delay(100);
          lcd.setCursor(0, 3);
          lcd.print("START");
          delay(200);
          if (digitalRead(buttonDOWN) == LOW) {
            cursor = 2;
          }
        }
      }
      if (cursor == 2) {
        menu = 1;
      }
      if (cursor == 1) {
        menu = 0;
      }
    }

    if (menu == 22 || menu == 23) {          ///////////////////////////////////////////////// 2.2 Load Program OR 2.3. Mod Program
      cursor = 1;
      val = 1;
      while (val != 0) {
        if (val == 1) {
          lcd.clear();
          lcd.setCursor(0, 0);
          if (menu == 22) {
            lcd.print("Load Program 1-3");
          }
          if (menu == 23) {
            lcd.print("Modify Program 1-3");
          }
          for(int i=1;i<4;i++){
              lcd.setCursor(3, i);
              lcd.print(EEPROM.read(3 * i + 5));
              lcd.print(" / ");
              lcd.print(EEPROM.read(3 * i + 6));
              lcd.print(" / ");
              lcd.print(EEPROM.read(3 * i + 7));
          }
          while (digitalRead(buttonOK) == LOW) {
            delay(10);
          }
          while (digitalRead(buttonOK) == HIGH && cursor != 4 && cursor != 0) {
            lcd.setCursor(0, cursor);
            lcd.print("->");
            if (digitalRead(buttonDOWN) == LOW && cursor < 4) {
              lcd.setCursor(0, cursor);
              lcd.print("  ");
              cursor = cursor + 1;
              lcd.setCursor(0, cursor);
              if (cursor != 4) {
                lcd.print("->");
              }
              if (cursor == 4) {
                val = 2;
              }
              delay(300);
            }
            if (digitalRead(buttonUP) == LOW && cursor > 0) {
              lcd.setCursor(0, cursor);
              lcd.print("  ");
              cursor = cursor - 1;
              lcd.setCursor(0, cursor);
              if (cursor != 0) {
                lcd.print("->");
              }
              if (cursor == 0) {
                val = 4;
              }
              delay(300);
            }
          }
          if (digitalRead(buttonOK) == LOW) {
            val = 0;
          }
          if (cursor == 0) {
            cursor = 12;
          }

        }

        if (val == 2) {
          lcd.clear();
          lcd.setCursor(0, 0);
          if (menu == 22) {
            lcd.print("Load Program 4-6");
          }
          if (menu == 23) {
            lcd.print("Modify Program 4-6");
          }
          for(int i=4;i<7;i++){
              lcd.setCursor(3, i-3);
              lcd.print(EEPROM.read(3 * i + 5));
              lcd.print(" / ");
              lcd.print(EEPROM.read(3 * i + 6));
              lcd.print(" / ");
              lcd.print(EEPROM.read(3 * i + 7));
          }
          while (digitalRead(buttonOK) == HIGH && cursor != 3 && cursor != 7) {
            lcd.setCursor(0, cursor - 3);
            lcd.print("->");
            if (digitalRead(buttonDOWN) == LOW && cursor < 7) {
              lcd.setCursor(0, cursor - 3);
              lcd.print("  ");
              cursor = cursor + 1;
              lcd.setCursor(0, cursor - 3);
              if (cursor != 7) {
                lcd.print("->");
              }
              if (cursor == 7) {
                val = 3;
              }
              delay(300);
            }
            if (digitalRead(buttonUP) == LOW && cursor > 3) {
              lcd.setCursor(0, cursor - 3);
              lcd.print("  ");
              cursor = cursor - 1;
              lcd.setCursor(0, cursor - 3);
              if (cursor != 3) {
                lcd.print("->");
              }
              if (cursor == 3) {
                val = 1;
              }
              delay(300);
            }
          }
          if (digitalRead(buttonOK) == LOW) {
            val = 0;
          }
        }

        if (val == 3) {
          lcd.clear();
          lcd.setCursor(0, 0);
          if (menu == 22) {
            lcd.print("Load Program 7-9");
          }
          if (menu == 23) {
            lcd.print("Modify Program 7-9");
          }
          for(int i=7;i<10;i++){
              lcd.setCursor(3, i-6);
              lcd.print(EEPROM.read(3 * i + 5));
              lcd.print(" / ");
              lcd.print(EEPROM.read(3 * i + 6));
              lcd.print(" / ");
              lcd.print(EEPROM.read(3 * i + 7));
          }
          while (digitalRead(buttonOK) == HIGH && cursor != 6 && cursor != 10) {
            delay(100);
            lcd.setCursor(0, cursor - 6);
            lcd.print("->");
            if (digitalRead(buttonDOWN) == LOW && cursor < 10) {
              lcd.setCursor(0, cursor - 6);
              lcd.print("  ");
              cursor = cursor + 1;
              lcd.setCursor(0, cursor - 6);
              if (cursor != 10) {
                lcd.print("->");
              }
              if (cursor == 10) {
                val = 4;
              }
              delay(300);
            }
            if (digitalRead(buttonUP) == LOW && cursor > 6) {
              lcd.setCursor(0, cursor - 6);
              lcd.print("  ");
              cursor = cursor - 1;
              lcd.setCursor(0, cursor - 6);
              if (cursor != 6) {
                lcd.print("->");
              }
              if (cursor == 6) {
                val = 2;
              }
              delay(300);
            }
          }
          if (digitalRead(buttonOK) == LOW) {
            val = 0;
          }
        }

        if (val == 4) {
          lcd.clear();
          lcd.setCursor(0, 0);
          if (menu == 22) {
            lcd.print("Load Program 10-12");
          }
          if (menu == 23) {
            lcd.print("Modify Program 10-12");
          }
          for(int i=10;i<13;i++){
              lcd.setCursor(3, i-9);
              lcd.print(EEPROM.read(3 * i + 5));
              lcd.print(" / ");
              lcd.print(EEPROM.read(3 * i + 6));
              lcd.print(" / ");
              lcd.print(EEPROM.read(3 * i + 7));
          }
          while (digitalRead(buttonOK) == HIGH && cursor != 9 && cursor != 13) {
            delay(100);
            lcd.setCursor(0, cursor - 9);
            lcd.print("->");
            if (digitalRead(buttonDOWN) == LOW && cursor < 13) {
              lcd.setCursor(0, cursor - 9);
              lcd.print("  ");
              cursor = cursor + 1;
              lcd.setCursor(0, cursor - 9);
              if (cursor != 13) {
                lcd.print("->");
              }
              if (cursor == 13) {
                val = 1;
              }
              delay(300);
            }
            if (digitalRead(buttonUP) == LOW && cursor > 9) {
              lcd.setCursor(0, cursor - 9);
              lcd.print("  ");
              cursor = cursor - 1;
              lcd.setCursor(0, cursor - 9);
              if (cursor != 9) {
                lcd.print("->");
              }
              if (cursor == 9) {
                val = 3;
              }
              delay(300);
            }
          }
          if (cursor == 13) {
            cursor = 1;
          }
          if (digitalRead(buttonOK) == LOW) {
            val = 0;
          }
        }

      }


      if (menu == 22) {              //////////////////////////////////////////// Load Program
        val1 = EEPROM.read(3 * cursor + 5);
        val2 = EEPROM.read(3 * cursor + 6);
        val3 = EEPROM.read(3 * cursor + 7);
        val = 3 * cursor + 5;
        lcd.clear();
        lcd.setCursor(0, 0);
        lcd.print("Start Program?");
        lcd.setCursor(0, 1);
        lcd.print("-Photos: ");
        lcd.print(val1);
        lcd.setCursor(0, 2);
        lcd.print("-Angle:  ");
        lcd.print(val2);
        lcd.setCursor(0, 3);
        lcd.print("-Pos.:   ");
        lcd.print(val3);
        lcd.setCursor(17, 2); lcd.print("YES");
        lcd.setCursor(18, 3); lcd.print("NO");
        cursor = 2;
        while (digitalRead(buttonOK) == LOW) {
          delay(10);
        }
        while (digitalRead(buttonOK) == HIGH) {
          if (digitalRead(buttonUP) == LOW && cursor > 1) {
            cursor = cursor - 1;
          }
          if (digitalRead(buttonDOWN) == LOW && cursor < 2) {
            cursor = cursor + 1;
          }
          if (cursor == 1) {
            lcd.setCursor(17, 2);
            lcd.print("   ");
            delay(100);
            lcd.setCursor(17, 2);
            lcd.print("YES");
            delay(200);
          }
          if (cursor == 2) {
            lcd.setCursor(17, 3);
            lcd.print("   ");
            delay(100);
            lcd.setCursor(18, 3);
            lcd.print("NO");
            delay(200);
          }
        }
        if (cursor == 2) {
          menu = 1;
        }
        if (cursor == 1) {
          menu = 0;
          if (EEPROM.read(100) != EEPROM.read(val)) {
            EEPROM.write(100, EEPROM.read(val));
          }
          if (EEPROM.read(101) != EEPROM.read(val + 1)) {
            EEPROM.write(101, EEPROM.read(val + 1));
          }
          if (EEPROM.read(102) != EEPROM.read(val + 2)) {
            EEPROM.write(102, EEPROM.read(val + 2));
          }
        }
      }


      if (menu == 23) {                     //////////////////////////////////////// Modify
        val = 3 * cursor + 5;
        val1 = EEPROM.read(val);
        val2 = EEPROM.read(val + 1);
        val3 = EEPROM.read(val + 2);
        lcd.clear();
        lcd.setCursor(0, 0);
        lcd.print("Photos per Rotation:");
        lcd.setCursor(0, 1);
        lcd.print("current: ");
        lcd.print(val1);
        lcd.setCursor(0, 2);
        lcd.print("new:     ");
        while (digitalRead(buttonOK) == LOW) {
          delay(10);
        }
        while (digitalRead(buttonOK) == HIGH) {
          if (digitalRead(buttonDOWN) == LOW && val1 >= 8) {
            val1 = val1 / 2;
          }
          if (digitalRead(buttonUP) == LOW && val1 < 128) {
            val1 = val1 * 2;
          }
          lcd.setCursor(10, 2);
          lcd.print("   ");
          lcd.setCursor(9, 2);
          lcd.print(val1);
          delay(200);
        }

        lcd.clear();
        lcd.setCursor(0, 0);
        lcd.print("Start at Angle:");
        lcd.setCursor(0, 1);
        lcd.print("current: ");
        lcd.print(val2);
        lcd.setCursor(0, 2);
        lcd.print("new:     ");
        while (digitalRead(buttonOK) == LOW) {
          delay(10);
        }
        while (digitalRead(buttonOK) == HIGH) {
          if (digitalRead(buttonDOWN) == LOW && val2 > 0) {
            val2 = val2 - 1;
          }
          if (digitalRead(buttonUP) == LOW && val2 < 75) {
            val2 = val2 + 1;
          }
          lcd.setCursor(10, 2);
          lcd.print("   ");
          lcd.setCursor(9, 2);
          lcd.print(val2);
          delay(80);
        }

        lcd.clear();
        lcd.setCursor(0, 0);
        lcd.print("Vert. Positions");
        lcd.setCursor(0, 1);
        lcd.print("current: ");
        lcd.print(val3);
        lcd.setCursor(0, 2);
        lcd.print("new:     ");
        while (digitalRead(buttonOK) == LOW) {
          delay(10);
        }
        while (digitalRead(buttonOK) == HIGH) {
          if (digitalRead(buttonDOWN) == LOW && val3 > 1) {
            val3 = val3 - 1;
          }
          if (digitalRead(buttonUP) == LOW && val3 < 32) {
            val3 = val3 + 1;
          }
          lcd.setCursor(10, 2);
          lcd.print("   ");
          lcd.setCursor(9, 2);
          lcd.print(val3);
          delay(200);
        }

        lcd.clear();
        lcd.setCursor(0, 0);
        lcd.print("Save new Program?");
        lcd.setCursor(0, 1);
        lcd.print("- Old: ");
        lcd.print(EEPROM.read(val));
        lcd.print("/");
        lcd.print(EEPROM.read(val + 1));
        lcd.print("/");
        lcd.print(EEPROM.read(val + 2));
        lcd.setCursor(0, 2);
        lcd.print("- New: ");
        lcd.print(val1);
        lcd.print("/");
        lcd.print(val2);
        lcd.print("/");
        lcd.print(val3);
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

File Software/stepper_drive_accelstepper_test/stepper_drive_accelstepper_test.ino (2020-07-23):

#include <AccelStepper.h>

AccelStepper stepper(1, 6, 7);
const int buttonPin = 3;
int buttonState = 0;
void setup() {
   // set up motor
   stepper.setEnablePin(5);
   stepper.setMaxSpeed(1600);
   stepper.setAcceleration(1600);
   stepper.setPinsInverted(true, false, true);
   stepper.moveTo(200000);

   pinMode(buttonPin, INPUT);
}

void loop() {
  // disable outputs is button pressed
  buttonState = digitalRead(buttonPin);
  if (buttonState == HIGH) {
    stepper.disableOutputs();
  }
  else {
    stepper.enableOutputs();
  }
  
  // If at the end of travel go to the other end
    if (stepper.distanceToGo() == 0)
      stepper.moveTo(-stepper.currentPosition());
    stepper.run();
}

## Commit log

2020-06-01 Adding docs & files from en.openscan.eu
    [Adapter1.stl, Adapter2_-_Gear_large.stl, Control_module.stl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]
2020-06-01 Modifying Stands to fit in my 3D Printer
    Will require glueing pieces together
    [Stand1_-_Nema17 - Short.stl, Stand1_-_Nema17 - Top.stl, Stand1_-_Nema17 v4.f3d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]
2020-06-08 Added png of wiring
2020-06-09 Adding stepper motor testing & moving files
2020-06-10 creation of accel stepper test
2020-07-23 Bug Fix
    Removed direct shutter option while trying to remove IR shutter for specific models
    [Scanner_Software_No_IRShutter.ino]
2020-07-23 Fixed bug
    Accidentially comment out shutter release time resulting in no photos being taken. Uncommented and worked
    [Scanner_Software_No_IRShutter.ino]
